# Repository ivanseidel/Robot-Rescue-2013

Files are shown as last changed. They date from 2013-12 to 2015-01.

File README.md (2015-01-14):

Robot-Rescue-2013
=================

RoboCup Rescue B

This repository includes the entire Rescue B project from 2013, used in the international RoboCup Rescue B league.

There is an old version (android based) of it (on the picture, the 2012 one), find out more [here](https://github.com/ivanseidel/Robot-Rescue-2012).

This robot uses two Arm Cortex M3 and one Atmega328. All the code is written in C++, using using Interfaces, and Classes hierarchy to provide well encapsulated code, and easy to use.

Because our team was participating at the same time on the Soccer Junior B league too, we couldn't finish it's code completely, but Mechanics, Hardware and Firmware part was 100% completed. Here is the [Soccer project repository](https://github.com/ivanseidel/Robot-Soccer-2013).

The image bellow is a picture/render of the real robot, and it's project rendered in SolidWorks.

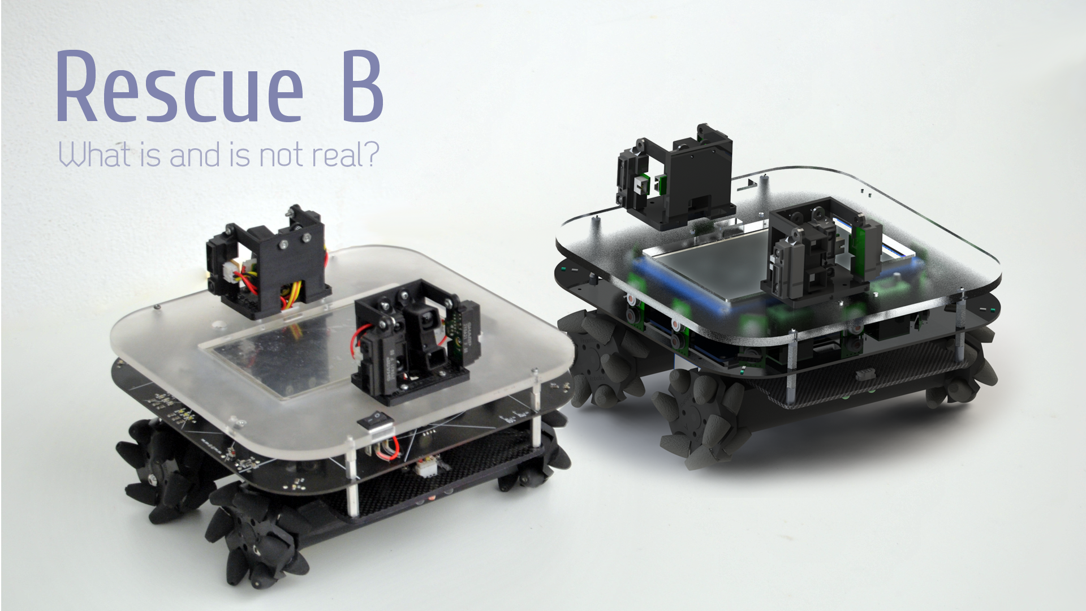
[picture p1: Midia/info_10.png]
RoboCup Rescue B render


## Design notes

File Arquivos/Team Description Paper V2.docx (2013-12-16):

Abstract— This paper presents a description of an omnidirectional robot to be used on the Rescue B competition. The main robot controller was written in C++ and runs in an Arduino DUE board. The Arduino board, that is responsible for the distance and temperature sensors readings, is connected to an MBed board that controls the motor drivers. There are eight infra-red distance sensors mounted on the top of the robot, four of them measuring the distance form the robot and the side walls, two measuring the distance in front of the robot and the other two measuring the distance from the back. The robot mechanical structure was designed using a 3D modeling software and was built using acrylic. It has four omnidirectional wheels that allow the robot to move in any direction without the need of turning itself. The robot was entirely designed, built and programmed by the team students.

# Team Description Paper: Team Emerotecos

Abílio Marcos Coelho de Azevedo¹, André Seidel Oliveira², Ivan Seidel Gomes³, Yan Victor Ribeiro Marim⁴ , Matheus Pimentel Canejo Pinheiro da Cunha⁵, Hudson Cássio Gomes Oliveira⁶, Felipe Nascimento Martins⁷

# I. Introduction

This is to show team Emerotecos’ strategies to solve the challenge proposed to the Rescue B Competition.

To build the robot, we didn’t use any building kit, as we designed the whole robot from sketch, using Dassault Systemes’ Solid Works software [1]. The robot was built basically with 5mm thick acrylic pieces, whose are tough enough for the application.

As the main processor, we use an Arduino DUE boad, which is programmed using C++. We choose the Arduino DUE board because, comparing to the Android mobile phone that we used last year, it is easier to communicate with the motors and sensors as the board has many analogic and digital entries, also using I2C protocol.

# II. Objective

The objective of this project is to build a smart robot that can cross a maze build with wood walls, and identify the electrically heated victims that are placed along the maze’s walls.

# III. Ambient

The Challenge happens in a modular arena, made with wood, which has 2 floors, and 4 main rooms. The location of the walls are always unknown by the time the robot starts running, so that it runs in a real maze. The only constant information about the arena is its total size, what makes it easier to the robot to find its way on the place. An illustration of the maze is shown in Figure 1.

Some heated “victims” are randomly positioned on some walls in the arena, and the robot has to identify them to get points.

In some places, there are some “dead ends”, which are a black mat on the ground. The robot can run over these black mats, but it has to leave it on the same side it came from, it can’t cross the black area.

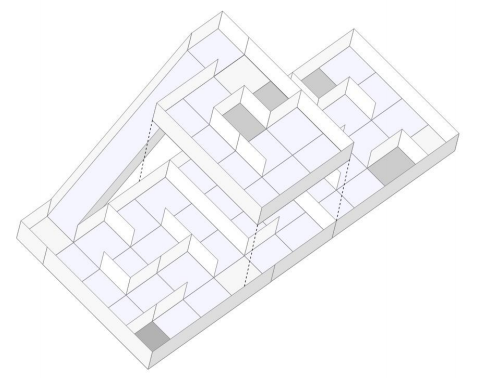
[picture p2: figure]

Rescue B Arena illustration.

# IV. Strategy

## A. Robot Structure

As we participated in this category last year, we built it basically like our first version(figure 4), but with some important improvements that will ensure a better performance is this competition. The robot´s basic composition are 2 acrylic layers, and some acrylic beams. We use a Mecanum omnidirectional wheels system, which makes our robot able to drive to every direction. The Mecanum system works as a regular omni system, and now we´re going to try new suspensions (figure 2) to hold the motors, made of kevlar. Figure 3 shows the robot eletronics design and Figure 1 shows the actual robot.

We use 4 very strong motors, with encoders, so that we can precisely move our robot everywhere. We rely on 4 motors, one for each wheel, because the MECANUM omnidirectional system need different control for each wheel. Each motor can spin giving a 6kgm torque, and its encoder can read up to 3592 pulses per turn because we have a 75:1 speed reduction.


Figure 1 - This year´s Robot

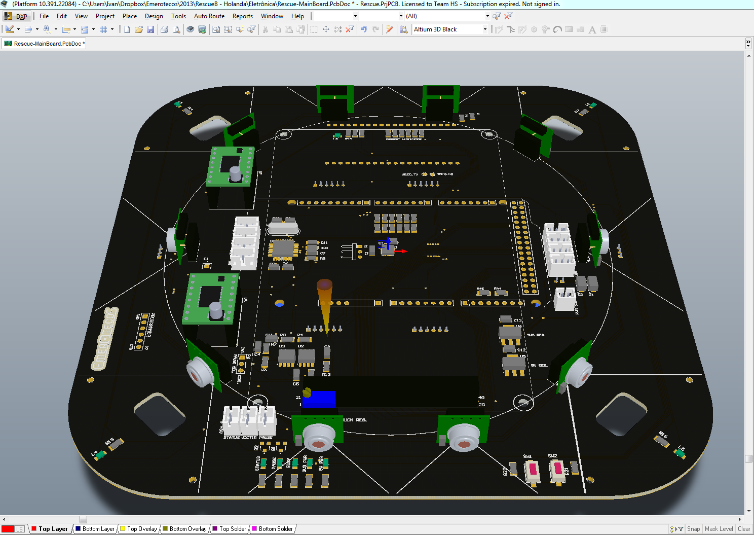
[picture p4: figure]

Figure 3 - Eletronics.

To process the encoder pulses, we have a MBED board, using a ARM Cortex M3, at 100MHz. This board is also responsible for controlling the engines speed. The communication protocol used to read the encoders from the interface, and to set the motors speeds, is the I²C. The MBED board only has 3 encoder inputs. So, we had to program another encoder counter.

To make good measurements with the infrared distance sensors, we’ve made two supports that will accomodade them in the front and back of the robot, to get measurements in every direction. Each support will carry four sensors.

As we use complex algorithms (described latter), we need a very complex processing unit. For this reason we have decided to use an Arduino Due instead of the Android phone used on our last robot. We chose Arduino because its communication with the other controlling systems will be faster. Also, we have an independent touchscreen LCD screen and several sensors, like IMU, so that we can replace the Android facilities. Our sensors gives the robot a very precise way to know it’s position and angle, on all axles, so that we can execute our mapping device with precision and reliability.

As you can see in the Figures 2 and 3, the distance sensors are positioned on rotary base on the top of the robot. This base is driven by a servomotor so that the sensors can be aimed to virtually any direction. Its visible too how are the Mecanum wheels mounted on the robot, similar to a Four by Four car, but with the capacity of moving to any direction without needing to turn.


Figure 2 - Suspension pressure test

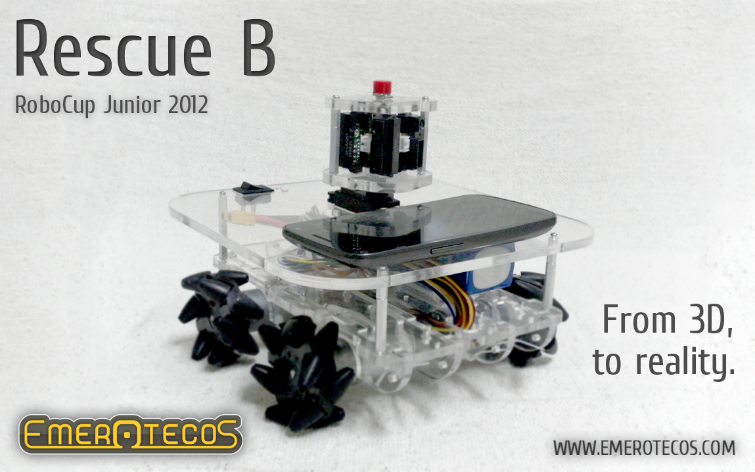
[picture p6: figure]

Figure 4 - Last year robot

## B. Programming

The main controller of our robot is an Arduino Due, witch process the main code and receives information from distance sensors so that it can send the orders to the MBED, that controls the motors.

Last year, the Android phone were used to send and receive data to/from the IOIO, which reads the sensors, and communicates with the MBED board, the one responsible for controlling the motors. Turned out that this configuration was overloading the communication system, so with Arduino we could just take the IOIO board and make a faster contact between sensors and the processing.

Our robot uses 2 types of distance sensors: short distance sensors and long distance ones. That way we can be more precise at taking measurements by the front an back of the robot, as in figure 5.

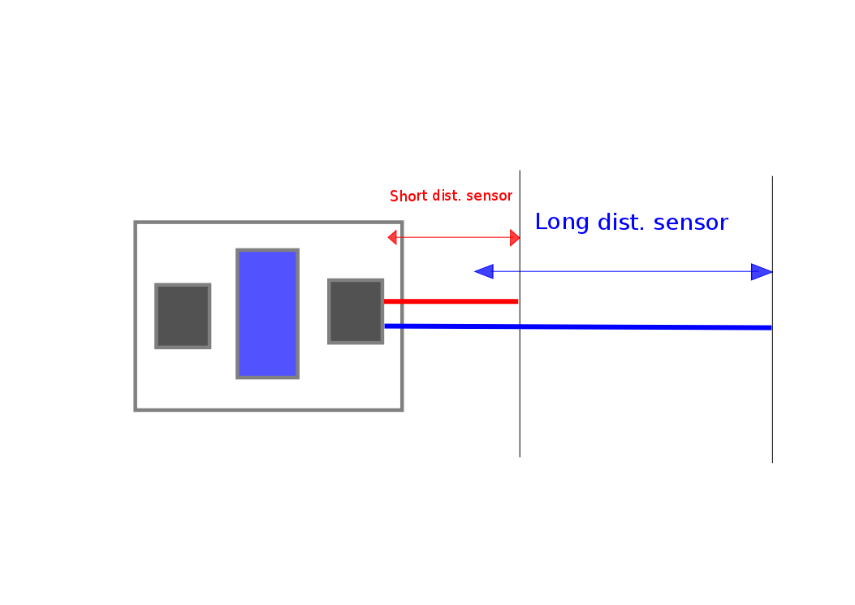
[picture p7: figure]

Figure 5 – Front/back sensors displacement

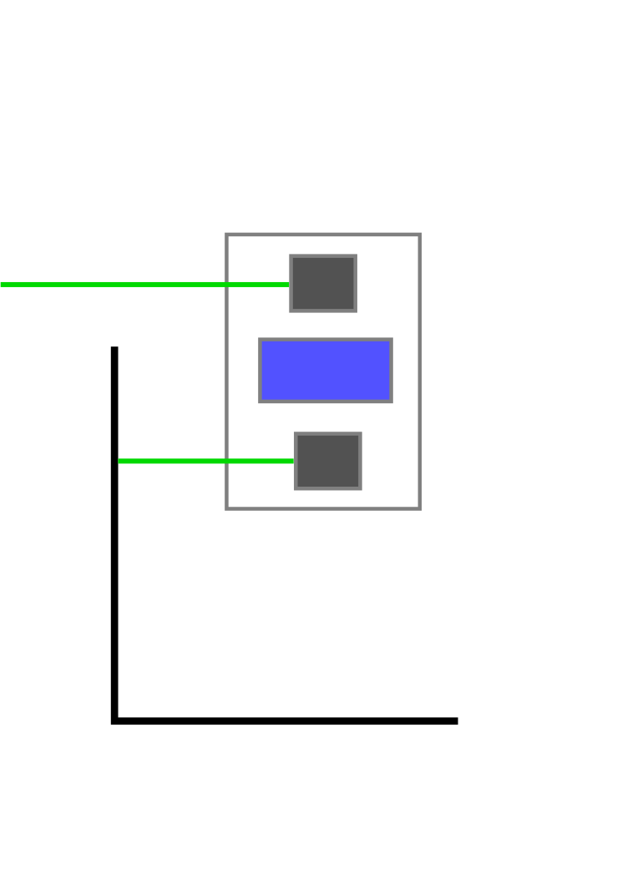
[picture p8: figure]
A description...

We also have heat sensors to detect victims all along the robot borders. The reason of choosing the front/back formation for the sensors supports is because that way the robot will know more accurately the end of any set of walls (figure 6) , so they need to be as far as they can be from each other.

Figure 6 – lateral sensors displacement

The distance measures are also used to correct the robot alignment in order to maintain its correct orientation parallel to the maze walls. This is done by comparing the measures at 20º and -20º from the central line, and calculating the necessary robot turning to make the robot alignment.

To move the robot, we use a simplified kind of SLAM (Simultaneous Localization And Mapping) algorithm, so that we can map the arena. We know that the walls are oriented in only 2 directions (0º and 90º), and we also know that each part of the maze is formed by a 30 x 30 cm square. With this knowledge and using the distance measures obtained via the infrared sensors, we can find out the walls positions and build a map of the maze. The SLAM is programmed in C++, and it runs on the Arduino DUE while the robot is moving in the arena.

We intend to change the algorithm to implement obstacle avoidance and to improve motion control. The idea is to make the robot move continually, with no stops. Last year´s robot succeeded to map, as in Figure 7, but on each block it had to stop, so we are trying to avoid it now. We also intend to attach more heat sensors. Those improvements will be completed by June 2013 for the RoboCupJunior 2013, in Holland.

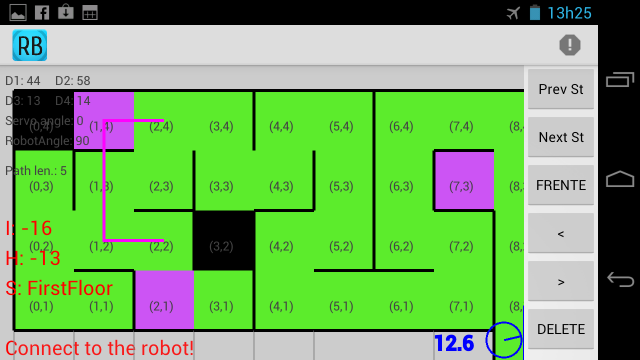
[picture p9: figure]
A description...

Figure 7 - On-line mapping from last year´s robot.

# V. Conclusion

Mapping is the best way to solve this challenge, because it makes it easy to visit every module of the arena, and consequently, find all victims. We have successfully used this robot in the RoboCupJunior 2012 Rescue B competition. A presentation video about the robot is available in [5].

# VI. Acknowledgement

The authors thank the Federal Institute from Espírito Santo (IFES) for all the support given in this project.

# References

[1] 3D CAD Design Software SolidWorks. Available at: http://www.solidworks.com/. Access: Sep. 5, 2012.
[2] Andoid, the world’s most popular mobile platform. Available at: http://developer.android.com/about/index.html. Access: Sep. 5, 2012.
[3] Mbed - Rapid Prototyping for Microcontrollers. Available at: http://mbed.org/. Access: Sep. 5, 2012.
[4] IOIO Documentation. Available at: https://github.com/ytai/ioio/wiki. Access: Sep 5, 2012.
[5] NERA. Prêmio de Melhor Robô do mundo é de alunos do IFES! (com vídeo). Available at http://nera.sr.ifes.edu.br/?p=143. Access: Sep. 5, 2012.

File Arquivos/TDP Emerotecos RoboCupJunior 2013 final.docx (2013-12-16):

# Team Description Paper: Team Emerotecos

Abílio Marcos Coelho de Azevedo, André Seidel Oliveira, Ivan Seidel Gomes, Yan Victor Ribeiro Marim , Matheus Pimentel Canejo Pinheiro da Cunha, Hudson Cássio Gomes Oliveira, Felipe Nascimento Martins

IFES – Federal Institute of Education, Science and Technology of Espirito Santo, Brazil

NERA – Núcleo de Estudos em Robótica e Automação

Abstract— This paper presents a description of an omnidirectional robot to be used on the RoboCupJunior Rescue B competition. The main robot controller was written in C++ and runs in an Arduino DUE board. The Arduino board is responsible for the distance and temperature sensors readings, and is connected to an MBed board that controls the motor drivers. There are eight infra-red distance sensors mounted on the top of the robot, four of them measuring the distance from the robot to the side walls, two measuring distance to obstacles or walls in front of the robot and the other two measuring distance to obstacles or walls in the back. The robot mechanical structure was designed using a 3D modeling software and was built using acrylic. It has four omnidirectional wheels that allow the robot to move in any direction without the need of turning itself. The robot was entirely designed, built and programmed by the team students.

# 1. Introduction

This is to show team Emerotecos’ strategies to solve the challenge proposed by the RoboCupJunior Rescue B competition.

To build the robot, we didn’t use any building kit, as we designed the whole robot from sketch, using Dassault Systemes’ Solid Works software [1]. The robot was built basically with 5mm thick acrylic and carbon fiber pieces, that we found are tough enough for the application.

As the main processor, we use an Arduino DUE board [2], which is programmed using C++. We choose the Arduino DUE board because, comparing to the Android mobile phone that we have used last year, it communicates faster with the motors and sensors as the board has many analogic and digital inputs. It also has support for I²C protocol, which we are using.

# 2. Objective

The objective of this project is to build a smart robot that can cross a maze build with wood walls, and identify the electrically heated victims that are placed along the maze’s walls.

# 3. Ambient

The Challenge happens in a modular arena, made with wood, which has 2 floors, and 4 main rooms. The location of the walls are always unknown by the time the robot starts running, so that it runs in a real maze. The only constant information about the arena is its total size, which makes it easier to the robot to find its way on the place. An illustration of the arena is shown in Figure 1.

Some heated “victims” are randomly positioned on some walls in the arena, and the robot has to identify them in order to score.

In some places, there are some “dead ends”, which are a black mat on the ground. The robot can run over these black mats, but it has to leave it on the same side it came from, it can’t cross the black area.

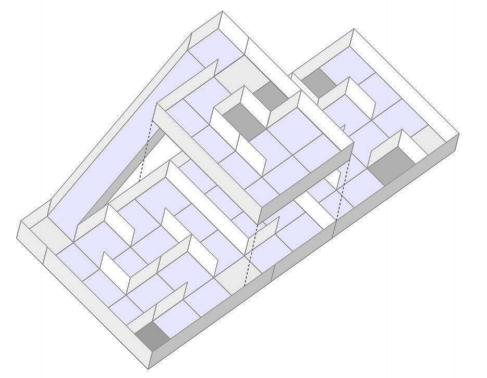
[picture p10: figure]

Fig. 1. Rescue B Arena illustration.

# 4. Strategy

## A. Robot Structure

We have participated in the Rescue B category last year. As our robot had a satisfactory performance, we have decided to build our new robot basically like our first version. Both robots are shown in Figure 2. Although the structure is the same, we have made some important improvements that we hope will ensure a better performance is this year’s competition. The robot’s basic structure is built with an acrylic layer and a carbon fiber layer, with some acrylic beams. We use a Mecanum omnidirectional wheels system, which makes our robot able to move in every direction. Four strong motors, with encoders, drive the robot very precisely. We rely on 4 motors, one for each wheel, because the MECANUM omnidirectional system need independent control for each wheel. Each motor has a torque of 6kgfm, and its encoder can read up to 3,592 pulses per turn because we have a 75:1 speed reduction.

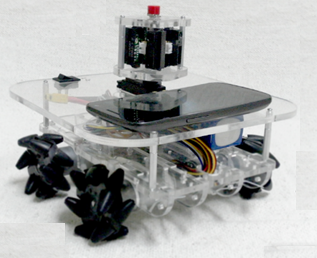
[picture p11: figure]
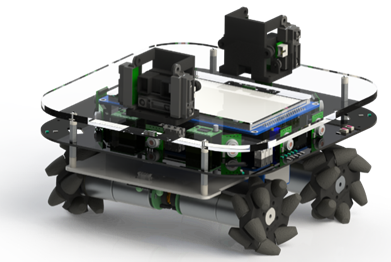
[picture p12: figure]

Fig.2. Last year’s robot (left) and this year´s robot (right).

The Mecanum system works as a regular omni system, and now we’re going to try a new suspension system to hold the motors. This is made of Kevlar and its design is illustrated in Figure 3.

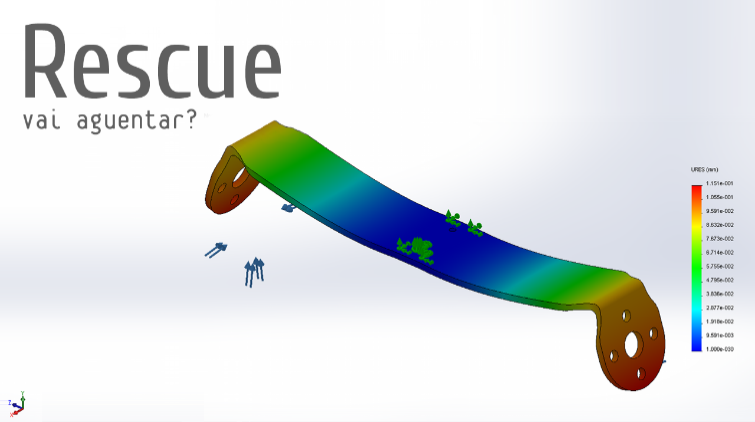
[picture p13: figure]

Fig. 3. Suspension bending simulation.

Figure 4 shows the robot electronics Printed Circuit Board (PCB) design, and Figure 5 presents the actual board already with the LCD placed on top of it. To process the encoder pulses, we have a MBED board [3], with ARM Cortex M3 processor, at 100MHz. This board is also responsible for controlling the motors speed. The communication protocol used to read the encoders from the interface, and to set the motors speeds, is the I²C. The MBED board only has 3 encoder inputs. So, we had to program another encoder counter.


Fig. 4. Eletronics PCB design.

To make good measurements with the infrared distance sensors, we’ve made two supports that will accommodate them in the front and back of the robot, to get measurements in every direction. Each support will carry four sensors.

As we use complex algorithms (described latter), we need a very complex processing unit. For this reason we have decided to use an Arduino Due instead of the Android phone used on our last robot. We chose Arduino because its communication with the other controlling systems will be faster. Figure 6 shows the bottom of the same board, where the Arduino Due and the MBED boards are placed.

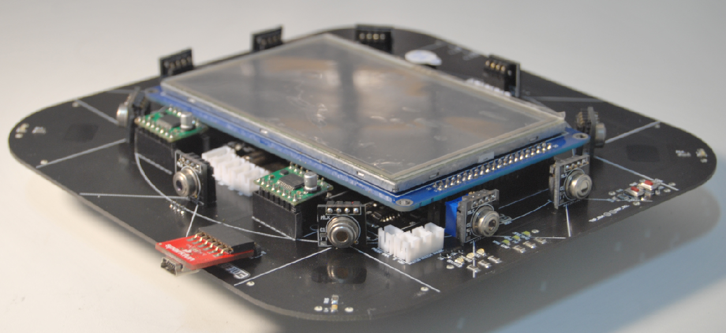
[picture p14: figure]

Fig. 5. Actual PCB (top) with heat sensors and LCD.

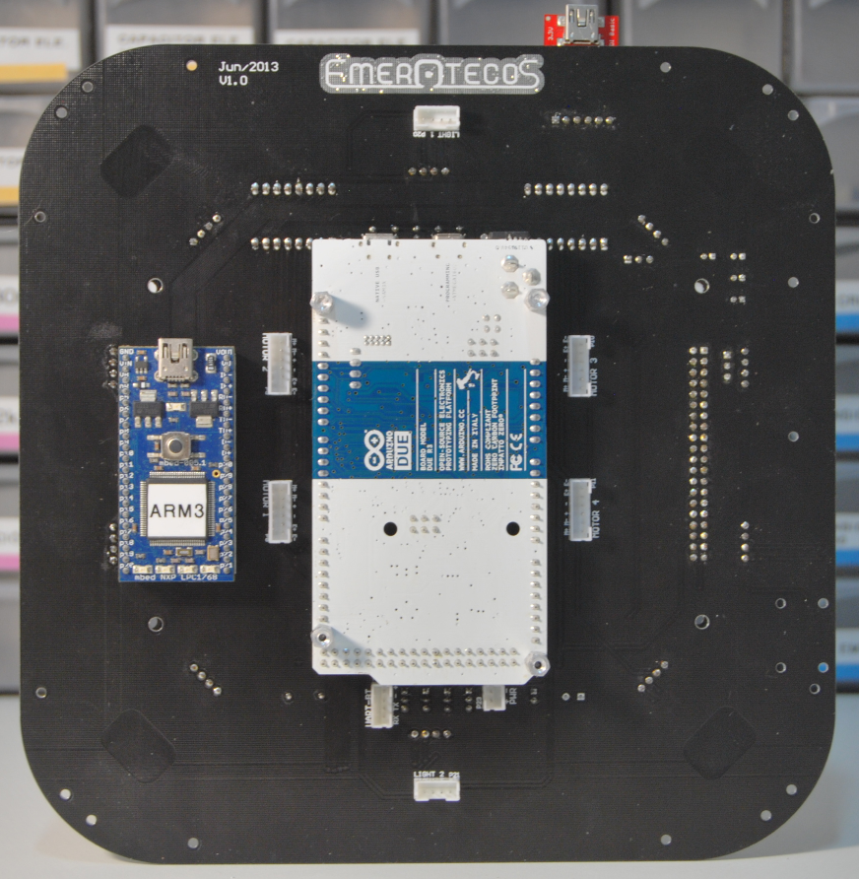
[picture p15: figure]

Fig. 6. Actual PCB (bottom) with Arduino Due and MBED boards.

## B. Programming

The main controller of our robot is an Arduino Due, witch process the main code and receives information from the distance sensors so that it can send commands to the MBED, which controls the motors.

Last year, an Android phone were used to send and receive data to/from an IOIO board [4], which reads the sensors, and communicates with the MBED board, the one responsible for controlling the motors. We have noticed that this configuration was overloading the communication system. To overcome this problem we are suing an Arduino Due instead of the Android phone, and we don’t need the IOIO board, which makes it faster to communicate with sensors and motors.

Our robot uses two types of infrared distance sensors: short distance sensors and long distance ones. Both types are mounted in front and in the back of the robot, pointing in the same direction. This was implemented to improve precision of the distance measurement in these directions (see Figure 7).


Fig. 7. Front/back sensors displacement

We also have heat sensors to detect victims all along the robot borders. The reason of choosing the front/back formation for the sensors supports is because that way the robot will know more accurately the end of any set of walls (figure 8), so they need to be as far as they can be from each other.

A description...

Fig. 8. Lateral sensors displacement

To move the robot, we use a simplified kind of SLAM (Simultaneous Localization And Mapping) algorithm, so that we can map the arena. We know that the walls are oriented in only 2 directions (0º and 90º), and we also know that each part of the maze is formed by a 30 x 30 cm square. With this knowledge and using the distance measures obtained via the infrared sensors, we can find out the walls positions and build a map of the maze. The SLAM is programmed in C++, and it runs on the Arduino DUE while the robot is moving in the arena.

We intend to change the algorithm to implement obstacle avoidance and to improve motion control. The idea is to make the robot move continually, with no stops. Last year´s robot succeeded to map, as shown in Figure 9, but on each block it had to stop to take distance measurements. We are trying to avoid this now. We also intend to attach more heat sensors. Those improvements will be completed by June 2013 for the RoboCupJunior 2013, in Holland.

A description...

Fig. 9. On-line mapping from last year´s robot.

# 5. Conclusion

Mapping is the best way to solve this challenge, because it makes it easy to visit every module of the arena, and consequently, find all victims. We have successfully used this robot in the RoboCupJunior 2012 Rescue B competition. A presentation video about the robot is available in [5]. In RoboCupJunior 2013 Rescue B we intend to succeed in mapping the arena, but now with the SLAM algorithm!

# 6. Acknowledgement

The authors thank the Federal Institute from Espírito Santo (IFES) for all the support given in this project.

# 7. References

[1] 3D CAD Design Software SolidWorks. Available at: http://www.solidworks.com/. Access: Sep. 5, 2012.
[2] Arduino Due. Available at: http://arduino.cc/en/Main/ArduinoBoardDue . Access: Mar. 29, 2013.
[3] MBED - Rapid Prototyping for Microcontrollers. Available at: http://mbed.org/. Access: Sep. 5, 2012.
[4] IOIO Documentation. Available at: https://github.com/ytai/ioio/wiki. Access: Sep 5, 2012.
[5] NERA. Prêmio de Melhor Robô do mundo é de alunos do IFES! (com vídeo). Available at http://nera.sr.ifes.edu.br/?p=143. Access: Sep. 5, 2012.

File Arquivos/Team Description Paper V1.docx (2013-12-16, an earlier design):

[^1]

# Team Description Paper: Team Emerotecos

Abílio Marcos Coelho de Azevedo¹, André Seidel Oliveira², Ivan Seidel Gomes³, Matheus Pimentel Canejo Pinheiro da Cunha⁴, Hudson Cássio Gomes Oliveira⁵, Felipe Nascimento Martins⁶

Abstract— This paper presents a description of an omnidirectional robot to be used on the Rescue B competition. The main robot controller was written in Java and runs in an Android-based mobile phone. The phone is connected to an IOIO board that serves as an interface between the main controller and the robot’s motors and sensors. The IOIO board connects to an Arduino board, that is responsible for the distance and temperature sensors readings, and to an MBed board that controls the motor drivers. There are four infra-red distance sensors mounted on a rotary base on the top of the robot. The base angle is constantly changed by a servomotor, which allows a 360º distance measuring. The robot mechanical structure was designed using a 3D modeling software and was built using acrylic. It has four omnidirectional wheels that allow the robot to move in any direction without the need of turning itself. The robot was entirely designed, built and programmed by the team students.

# I. Introduction

This is to show team Emerotecos’ strategies to solve the challenge proposed to the Rescue B Competition.

To build the robot, we didn’t use any building kit, as we designed the whole robot from sketch, using Dassault Systemes’ Solid Works software [1]. The robot was built basically with 5mm thick acrylic pieces, whose are tough enough for the application.

As the main processor, we use an Android phone, which is programmed using Java. This is a very interesting platform to work with since nowadays Android is the world’s most popular mobile platform [2].

To send the signals from the Android to the motors (that are controlled by an MBED board [3]), we use a board called IOIO, which is responsible for reading all the sensors as well [4].

# II. Objective

The objective of this project is to build a smart robot that can cross a maze build with wood walls, and identify the electrically heated victims that are placed along the maze’s walls.

# III. Ambient

The Challenge happens in a modular arena, made with wood, which has 2 floors, and 4 main rooms. The location of the walls are always unknown by the time the robot starts running, so that it runs in a real maze. The only constant information about the arena, is its total size, what makes it easier to the robot to find its way on the place. An illustration of the maze is shown in Figure 1.

Some heated “victims” are randomly positioned on some walls in the arena, and the robot has to identify them to get points.

In some places, there are some “dead ends”, which are a black mat on the ground. The robot can run over these black mats, but it has to leave it on the same side it came from, it can’t cross the black area.


Figure 1.  Rescue B Arena illustration.

# IV. Strategy

## A. Robot Structure

Our robot is built basically with 2 acrylic layers, and some acrylic beams. We use a Mecanum omnidirectional wheels system, which makes our robot able to drive to every direction. The Mecanum system works as a regular omni system, but it uses 4 tractioned wheels, instead of three, normally used. Figure 2 shows the robot design and Figure 3 shows the actual robot, without the control boards.

We use 4 very strong motors, with encoders, so that we can precisely move our robot everywhere. We rely on 4 motors, one for each wheel, because the MECANUM omnidirectional system need dierent control for each wheel. Each motor can spin giving a 6kgm torque, and its encoder can read up to 3592 pulses per turn because we have a 75:1 speed reduction.

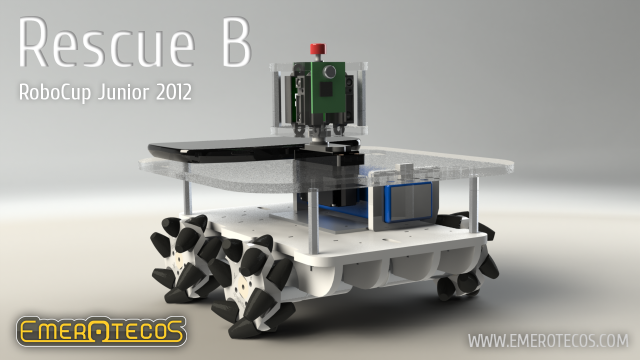
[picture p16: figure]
Info_05

Figure 1.  Robot design.

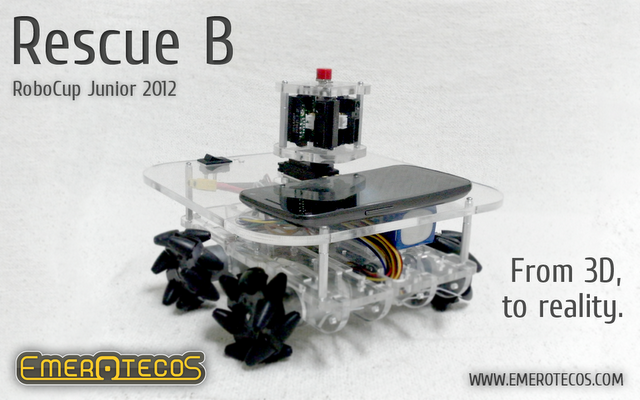
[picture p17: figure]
Info_06

Figure 2.  Robot picture(without control boards).

To process the encoder pulses, we have a MBED board, using a ARM Cortex M3, at 100MHz. This board is also responsible for controlling the engines speed. The communication protocol used to read the encoders from the interface, and to set the motors speeds, is the I²C. The MBED board only has 3 encoder inputs. So, we had to program another encoder counter.

To make good measurements with the infrared distance sensors, we’ve put them in a turnable head over the robot, so that we can make meausures to every direction. To identify the victims, we have 4 thermal infrared sensors strategically positioned around the robot, so that we can measure temperatures in every wall.

As we use complex algorithms (described latter), we need a very complex processing unit. For this reason we have decided to use an Android phone on our robot. Android because we can program using Java. Also, the phone has a touchscreen LCD screen and several sensors we can access. For instance, we make use of the 3 axles gyroscope and 3 axles magnetometer that are present on the Android phone. This gives the robot a very precise way to know it’s position and angle, on all axles.

As you can see in the Figures 2 and 3, the distance sensors are positioned on rotary base on the top of the robot. This base is driven by a servomotor so that the sensors can be aimed to virtually any direction. Its visible too how are the Mecanum wheels mounted on the robot, similar to a Four by Four car, but with the capacity of moving to any direction without the need to turn.

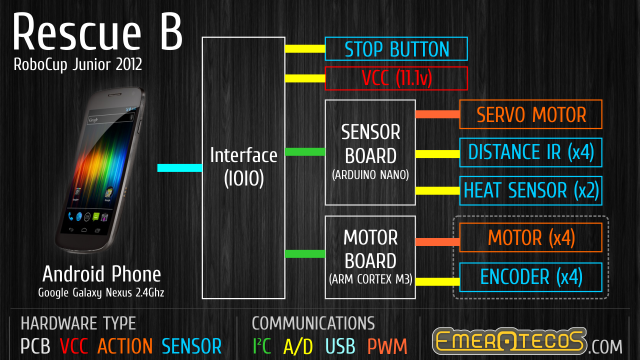
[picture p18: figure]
Info_04

Figure 3.  Control System overview.

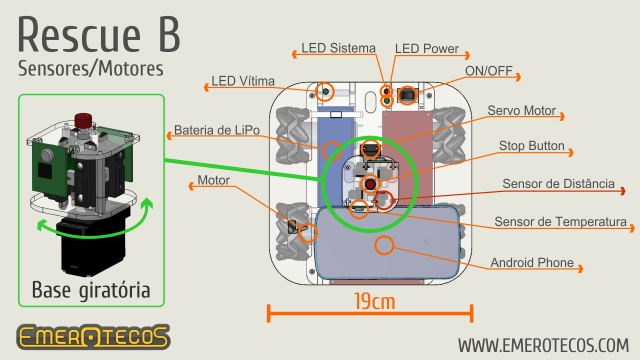
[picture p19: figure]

Figure 4.  Rotary base (left) and top view of the robot.

## B. Programming

The main controller of our robot is an Android cellphone. We choose Android, because it’s an open platform [2], and it’s possible to connect the cellphone with the sensors easily, using the IOIO board [4].

The Android phone sends and receives data to/from the IOIO, which reads the sensors, and communicates with the MBED board, the one responsible for controlling the motors. Figure 4 shows the control system overview.

Our robot uses 2 types of sensors: infrared distance sensor (by Sharp) and heat sensor. The heat sensor is used to detect the victims and are placed on the robot borders. As explained on the previous section, the infrared sensors are mounted on a rotary base. Each one of infrared sensors are pointed 90º from each other in a way that the 4 distance measures can be made at once. The 4 distance measures are repeated several times during a head rotation (one measure per degree) in order to detect the maze walls and obstacles. Figure 5 shows the rotary base with the infrared sensors placed on it, and presents a top view of the robot.

The distance measures are also used to correct the robot alignment in order to maintain its correct orientation parallel to the maze walls. This is done by comparing the measures at 20º and -20º from the central line, and calculating the necessary robot turning to make the robot alignment. Figure 6 illustrates the described idea.

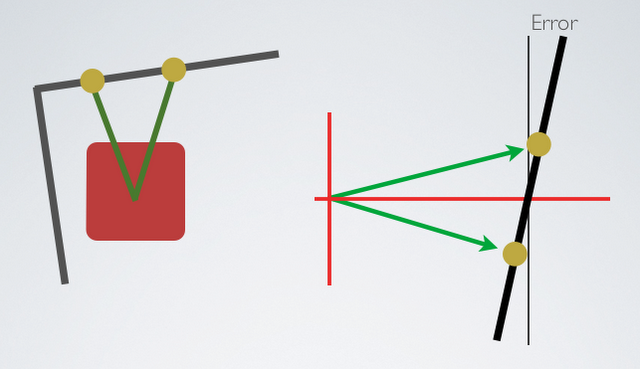
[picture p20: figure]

Figure 5.  Robot design.

To move the robot, we use a simplified kind of SLAM (Simultaneous Localization And Mapping) algorithm, so that we can map the arena. We know that the walls are oriented in only 2 directions (0º and 90º), and we also know that each part of the maze is formed by a 30 x 30 cm square. With this knowledge and using the distance measures obtained via the infrared sensors, we can find out the walls positions and build a map of the maze. The SLAM was programmed in JAVA, and it runs on the Android while the robot is moving in the arena.

While the robot walks around the arena, we can see the map being formed on the cellphone’s screen. Figure 6 shows an example of the mapping screen.


Figure 6.  On-line mapping.

# V. Conclusion

Mapping is the best way to solve this challenge, because it makes it easy to visit every module of the arena, and consequently, find all victims. We have successfully used this robot in the RoboCupJunior 2012 Rescue B competition. A presentation video about the robot is available in [5].

We pretend to change the algorithm to work with obstacles and also do a big improvement on motion of the robot moving continually, with no stops. Attach more infrared distance sensors, well located on the robot, so that they don`t need to rotate.

Those improvement will be done until June 2013 for the RoboCupJunior in Holland.

# VI. Acknowledgement

The authors thank the following companies for the financial support that allowed the robot construction and participation at the 2012 RoboCup and CBR competitions: Proesi Componentes Eletrônicos, Nova Didacta, InTechno Desenvolvimento e Capacitação, Copy Express, Produtiva Hailtools, Use Móveis para Escritórios and Qualidata. They also thank IFES for the support and FAPES (a foundation of the Secretary of Science and Technology of the State of Espirito Santo, Brazil) for the financial support to pay for the air tickets and travel expenses to Fortaleza – LARC 2012 (Project 57768773/2012).

# References

[1] 3D CAD Design Software SolidWorks. Available at: http://www.solidworks.com/. Access: Sep. 5, 2012.
[2] Andoid, the world’s most popular mobile platform. Available at: http://developer.android.com/about/index.html. Access: Sep. 5, 2012.
[3] Mbed - Rapid Prototyping for Microcontrollers. Available at: http://mbed.org/. Access: Sep. 5, 2012.
[4] IOIO Documentation. Available at: https://github.com/ytai/ioio/wiki. Access: Sep 5, 2012.
[5] NERA. Prêmio de Melhor Robô do mundo é de alunos do IFES! (com vídeo). Available at http://nera.sr.ifes.edu.br/?p=143. Access: Sep. 5, 2012.

[^1] The authors are with the Federal Institute of Education, Science and Technology of Espírito Santo (IFES). Rodovia ES-010, km 6,5 - Manguinhos, Serra, ES. abilio_azevedo@hotmail.com¹, aseideloliveira@gmail.com², ivanseidel@gmail.com³, pimentelcanejo@hotmail.com⁴, hudsoncassio@ifes.edu.br⁵, felipemartins@ifes.edu.br⁶.

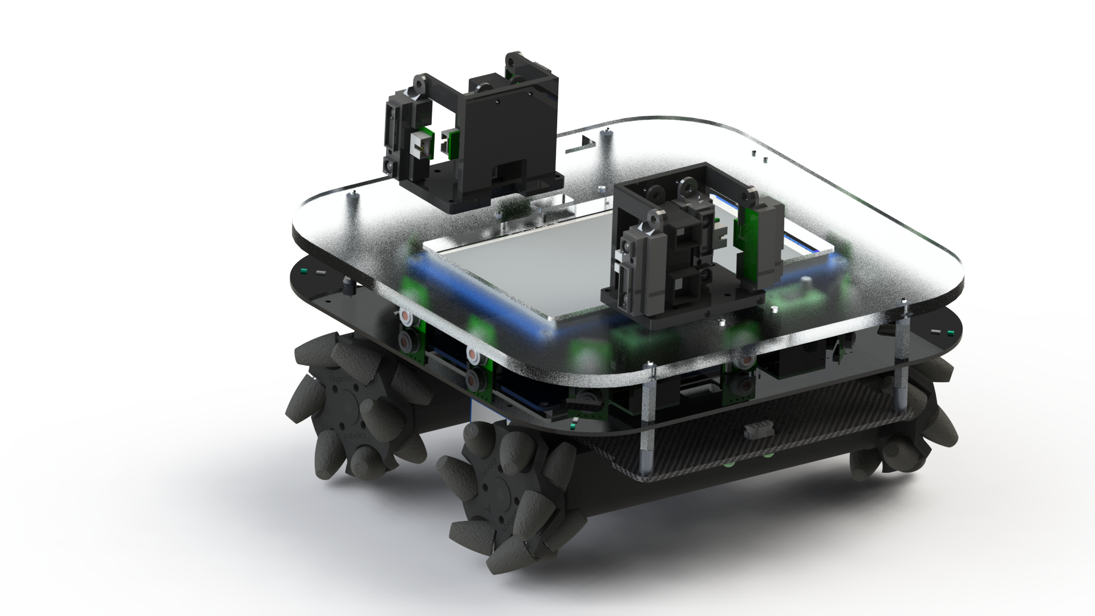
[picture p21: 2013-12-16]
Midia/robot_07.tif

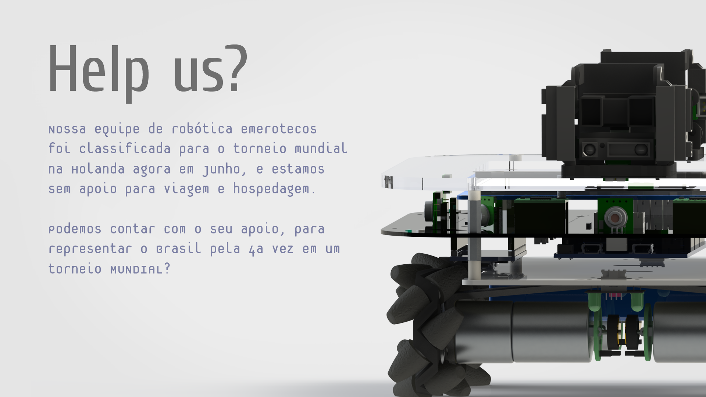
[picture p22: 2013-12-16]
Midia/info_07.png

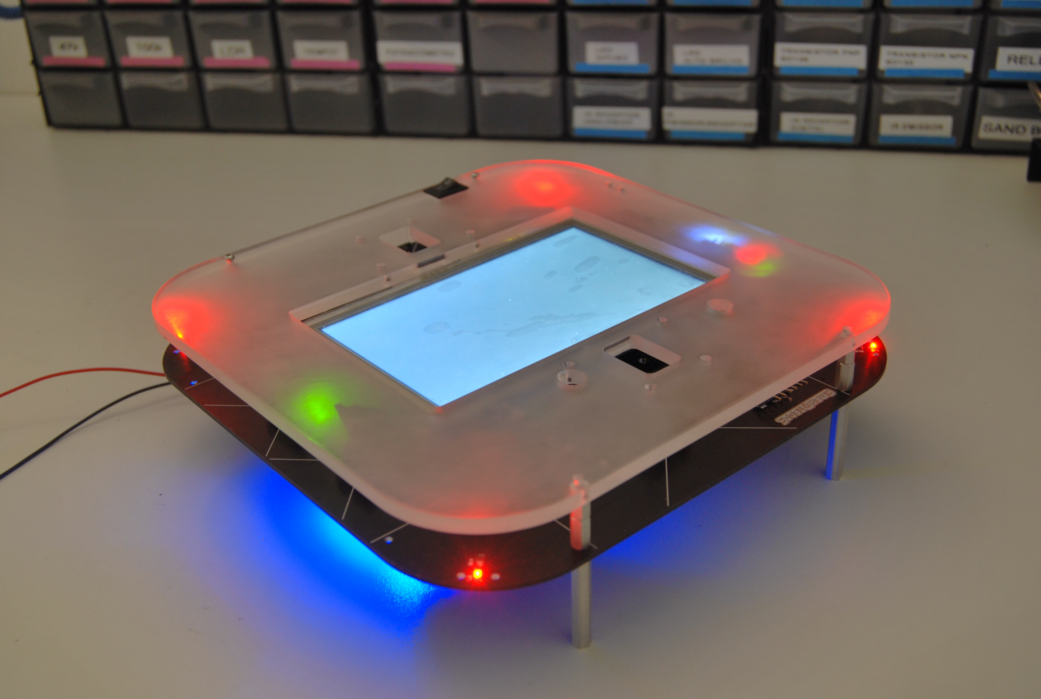
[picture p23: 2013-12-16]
Midia/Fotos/RescueB (19).JPG

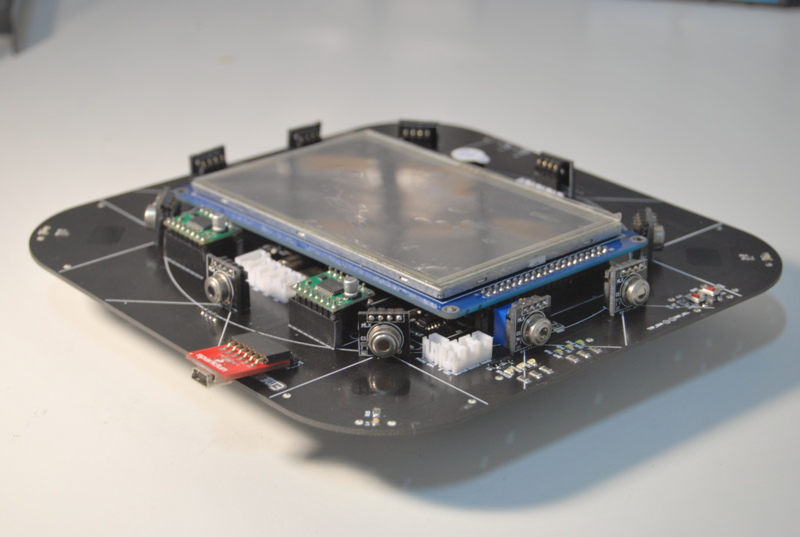
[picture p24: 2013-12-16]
Midia/Fotos/RescueB (8).JPG

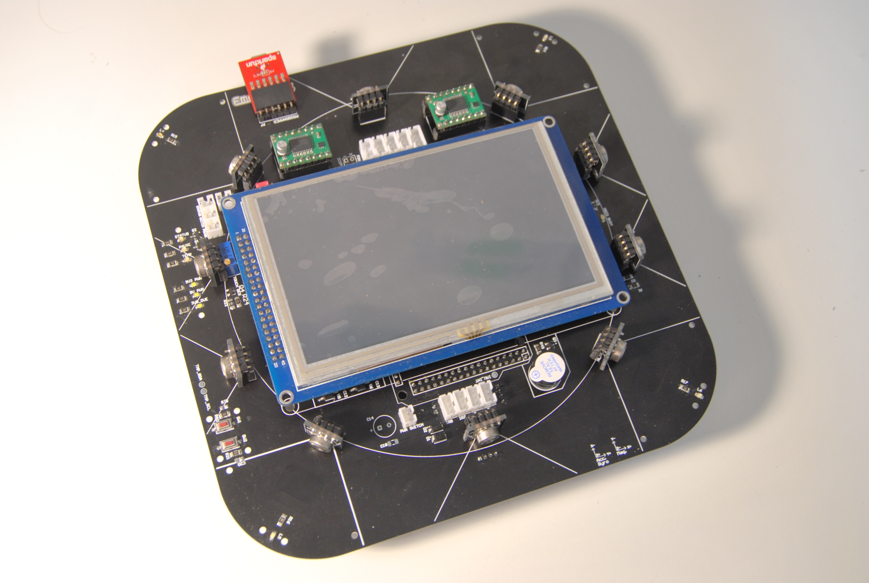
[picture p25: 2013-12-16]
Midia/Fotos/RescueB (6).JPG

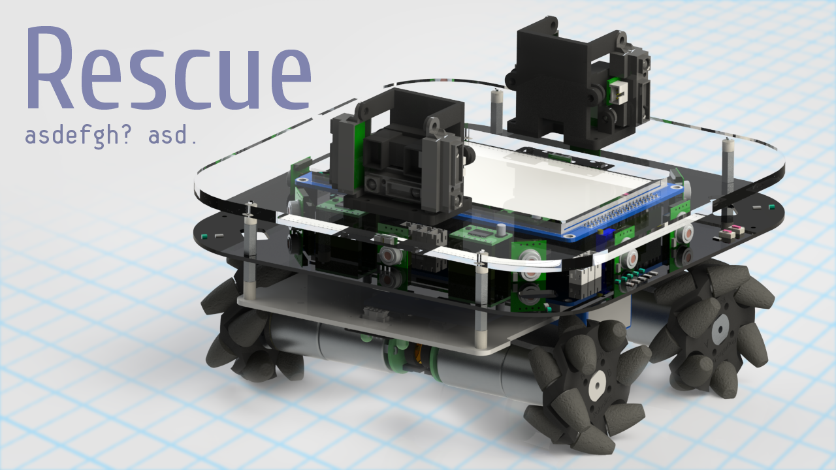
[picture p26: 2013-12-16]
Midia/info_06.png

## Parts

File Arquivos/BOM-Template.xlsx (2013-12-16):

PLANILHA DE CUSTOS - RESCUE B 2013 |  |  |  |  |  | TOTAL | R$3151.81
 |  |  |  |  |  | Dolar: | $2.20
Descrição | Fornecedor | Qtd | Extra | Valor | Imposto | Dolar? | Subtotal | Link
Standoffs (13 mm) FF | pololu | 3 | 1 | 1.79 | 70% | s | R$26.78 | http://www.pololu.com/catalog/product/2091
Standoffs (13 mm) MF | pololu | 3 | 1 | 1.39 | 70% | s | R$20.79 | http://www.pololu.com/catalog/product/1948
LCD TFT 5" | Dealextreme | 0 | 1 | 54.50 | 70% | s | R$203.83 | http://dx.com/p/800-x-480-5-0-lcd-tft-touch-screen-module-w-stylus-pen-for-arduino-blue-154505
Capacitores, Resistores, Transistores, IC's (Faltantes) | Dealextreme | 1 | 0
Bateria Lipo 1.6A 40C 2S 7.4v | HobbyKing | 4 | 0 | 9.49 | 70% | s | R$141.97 | http://www.hobbyking.com/hobbyking/store/__10278__Turnigy_2200mAh_2S_40C_Lipo_Pack.html
IMU InveSense (MPU-9150) | InveSense | 1 | 1 | 17.00 | 70% | s | R$127.16 | http://www.invensense.com/mems/gyro/mpu9150.html
Shipping | InveSense | 1 | 0 | 53.95 | 70% | s | R$201.77
xBee | Itead | 1 | 1 | 13.20 | 70% | s | R$98.74 | http://dx.com/p/xbee-arduino-bluetooth-wireless-module-with-bee-adapter-136423
Circuito Impresso - 10 unidades, 20cm x 20cm, Dupla Face, 1.6mm | Itead | 1 | 0 | 114.00 | 70% | s | R$426.36 | http://imall.iteadstudio.com/open-pcb/pcb-prototyping/im120418010.html
Circuito (para sensores de temp.) - 5cm x 5cm | itead | 1 | 0 | 15.00 | 70% | s | R$56.10 | http://imall.iteadstudio.com/open-pcb/pcb-prototyping/im120418004.html
Rodas Omni | Matheus | 8 | 1 | 0.00 |  |  | R$0.00
Base em alumínio | Matheus | 2 | 2 | 0.00 |  |  | R$0.00
Motores 25D (34:1) | Pololu | 4 | 1 | 34.95 | 70% | s | R$653.57 | http://www.pololu.com/catalog/product/2284 (http://www.pololu.com/catalog/product/1572)
Capacitores, Resistores, Transistores, IC's (Patrocínio) | Proesi | 0 | 0 | 0.00 |  |  | R$0.00
Arduino DUE | SparkFun | 1 | 1 | 49.95 | 70% | s | R$373.63 | https://www.sparkfun.com/products/11589
Mbed | SparkFun | 0 | 1 | 59.95 | 70% | s | R$224.21 | https://www.sparkfun.com/products/9564
Sensor Temp. | Sparkfun | 7 | 1 | 19.95 | 70% | s | R$596.90 | https://www.sparkfun.com/products/9570

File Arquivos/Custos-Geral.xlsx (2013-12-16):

Gastos individuais | Valor por pessoa | Subtotal
Passagem | R$4000.00 | R$20000.00
Hospedagem | R$1500.00 | R$7500.00
Alimentação | R$1000.00 | R$5000.00
Transporte | R$100.00 | R$500.00
Camiseta | R$150.00 | R$750.00
Gastos gerais |  | Subtotal
Material de transporte |  | R$1000.00
Componentes e peças para o Robô |  | R$5000.00
Material de divulgação (Folders, Adesivos…) |  | R$250.00
 | Total: | R$40000.00
Registro | http://www.regonline.com/Register/Checkin.aspx?EventID=1198240
Hotel

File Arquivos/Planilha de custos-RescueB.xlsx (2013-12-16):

PLANILHA DE CUSTOS - RESCUE B 2014 |  |  |  |  |  |  | TOTAL | R$2941.73 |  | Pololu
 |  |  |  |  |  |  | Dolar: | $2.20 |  | R$1305.67
OK | Descrição | Fornecedor | Qtd | Extra | Valor | Imposto | Dolar? | Subtotal | Link
s | LCD TFT 5" | Dealextreme | 1 | 1 | 54.50 |  | s | R$239.80 | http://dx.com/p/800-x-480-5-0-lcd-tft-touch-screen-module-w-stylus-pen-for-arduino-blue-154505
s | Bluetooth | Dealextreme | 1 | 0 | 11.70 |  | s | R$25.74 | http://dx.com/p/bluetooth-master-uart-board-communication-module-blue-152175
s | Capacitores 0805 | Dealextreme | 2 | 0 | 7.60 |  | s | R$33.44 | http://dx.com/p/smd-0805-capacitors-white-20-x-30-pcs-152739
s | Capacitor 1206 10uF | Dealextreme | 1 | 0 | 4.80 |  | s | R$10.56 | http://dx.com/p/avx-1206-smd-10uf-16v-type-a-tantalum-capacitors-30-pcs-148546
s | Capacitores Eletrolitico | Dealextreme | 1 | 0 | 8.60 |  | s | R$18.92 | http://dx.com/p/2-2-470uf-electrolytic-capacitor-assortment-kit-16-50v-100-pcs-156107
s | Bateria Lipo 1.8A 40C 2S 7.4v | HobbyKing | 4 | 0 | 9.49 |  | s | R$83.51 | http://www.hobbyking.com/hobbyking/store/__10289__Turnigy_1800mAh_2S_40C_Lipo_Pack.html
s | Shipping | HobbyKing | 1 | 0 | 17.95 |  | s | R$39.49
s | IMU InveSense (MPU-9150) | InveSense | 1 | 1 | 17.00 | 70% | s | R$127.16 | http://www.invensense.com/mems/gyro/mpu9150.html
s | Shipping | InveSense | 1 | 0 | 53.95 | 70% | s | R$201.77
s | Circuito Impresso - 10 unidades, 20cm x 20cm, Dupla Face, 1.6mm | Itead | 1 | 0 | 114.00 | 70% | s | R$426.36 | http://imall.iteadstudio.com/open-pcb/pcb-prototyping/im120418010.html
s | Circuito (para sensores de temp.) - 5cm x 5cm | itead | 1 | 0 | 15.00 | 70% | s | R$56.10 | http://imall.iteadstudio.com/open-pcb/pcb-prototyping/im120418004.html
s | Shipping | Itead | 1 | 0 | 40.00 | 70% | s | R$149.60
s | Distance IR (4-40cm) | LabDeGaragem | 2 | 1 | 68.10 |  |  | R$204.30 | https://www.sparkfun.com/products/8959
s | Shipping | LabDeGaragem | 1 | 0 | 19.30 |  |  | R$19.30
s | Standoffs (9.5 mm) FF | Pololu | 1 | 2 | 1.69 | 70% | s | R$18.96 | http://www.pololu.com/catalog/product/2084
s | Standoffs (6 mm) MF | Pololu | 1 | 2 | 1.29 | 70% | s | R$14.47 | http://www.pololu.com/catalog/product/1940
s | Standoffs (10 mm) MF | Pololu | 1 | 2 | 1.29 | 70% | s | R$14.47 | http://www.pololu.com/catalog/product/1941
s | Motores 25D (34:1) | Pololu | 0 | 1 | 34.95 | 70% | s | R$130.71 | http://www.pololu.com/catalog/product/2286
s | Arduino DUE | Pololu | 0 | 1 | 49.95 | 70% | s | R$186.81 | http://www.pololu.com/catalog/product/2193
s | Mbed | Pololu | 0 | 0 | 59.00 | 70% | s | R$0.00 | http://www.pololu.com/catalog/product/2150
s | Sensor Temp. | Pololu | 5 | 3 | 19.95 | 70% | s | R$596.90 | http://www.pololu.com/catalog/product/1061
s | Distance IR (20-150cm) | Pololu | 2 | 1 | 14.95 | 70% | s | R$167.74 | http://www.pololu.com/catalog/product/1137
s | Shipping | Pololu | 1 | 0 | 46.95 | 70% | s | R$175.59
s | Capacitores, Resistores, Transistores, IC's (Patrocínio) | Proesi | 0 | 0 | 0.00 |  |  | R$0.00

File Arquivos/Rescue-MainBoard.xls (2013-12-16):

 |  | Rescue-MainBoard.PrjPCB | Rescue-MainBoard.PrjPCB |  |  | 03/04/2013
 |  | PLANILHA DE CUSTOS | Bill of Materials For Project [Rescue-MainBoard.PrjPCB] (No PCB Document Selected) |  |  |  |  |  |  |  | TOTAL | R$0.00
 |  |  |  |  |  |  |  |  |  |  | Dolar: | $2.20
Colunas1 | Colunas2 | LibRef | Footprint | Comment | Designator | Description | Quantity | Extra | Valor | Imposto | Dolar? | Subtotal | Link
 | s | LM358D | 751-02_N | LM358D | U3 | Dual Low-Power Operational Amplifier | 1 | 1 | 0.00
 | s | BUZZER | BUZZER | Buzzer | BZ1 | Buzzer | 1 | 0 | 0.00
s |  | Cap Semi | C0805 | 100nF | C19, C20 | Capacitor (Semiconductor SIM Model) | 2 |  | 0.00
s |  | Cap Semi | C0805 | 0.1uF | C1, C6, C7, C8, C15 | Capacitor (Semiconductor SIM Model) | 5 |  | 0.00
s |  | Cap Semi | C0805 | 2.2nF | C2 | Capacitor (Semiconductor SIM Model) | 1 |  | 0.00
s |  | Cap Semi | C0805 | 100pF | C3, C4, C5, C11 | Capacitor (Semiconductor SIM Model) | 4 |  | 0.00
s |  | Cap Semi | C0805 | 22pF | C9, C10 | Capacitor (Semiconductor SIM Model) | 2 |  | 0.00
s |  | Cap Semi | C0805 | 10nF | C16 | Capacitor (Semiconductor SIM Model) | 1 |  | 0.00
s |  | Cap Semi | C1206 | 10uF | C12, C13, C17, C18 | Capacitor (Semiconductor SIM Model) | 4 |  | 0.00
s |  | EKA00PB310J00 | CAPPR3.5-8X11.5 | 470uF | C14 | Aluminum Electrolytic Capacitor, Radial Style with Long Leads: 100uF, 63V | 1 |  | 0.00
s |  | DIODE | DIODESMA | 1N4004 | D1, D2 |  | 2 |  | 0.00
s |  | Header 3X2 | HDR2X3 | Header 3X2 | P26 | Header, 3-Pin, Dual row | 1 |  | 0.00
 | s | LED | LED0805 | LED | 3V3_1, 3V3_DUE, 5V_1, L1, L2, L3, L4, L5, L6, L7, L8 |  | 11 | 29 | 0.00
 | s | LM555CM | M08A_N | LM555CM | U2 | Timer, 8-pin Narrow SOIC | 1 | 2 | 0.00
 | s | LM1117IMPX-5.0/NOPB | MP04A_N | LM1117IMPX-5.0/NOPB | U5 | 800mA Low-Dropout Linear Regulator, 4-pin SOT-223, Pb-Free | 1 |  | 0.00
 | s | LM1117IMPX-3.3/NOPB | MP04A_N | LM1117IMPX-3.3/NOPB | U6 | 800mA Low-Dropout Linear Regulator, 4-pin SOT-223, Pb-Free | 1 |  | 0.00
 | s | OSC-2-PIN | OSC-2-PIN-TH | 16Mhz | Y1 | 2 pin oscilator | 1 |  | 0.00
s | s | RES | RES1206 | 10K | R1, R2, R5, R6, R9, R10, R12, R20, R21, R24, R32, R34, R36, R38, R40, R42, R44, R46, R47, R49 |  | 20 |  | 0.00
 | s | RES | RES1206 | 100K | R3, R4 |  | 2 |  | 0.00
 | s | RES | RES1206 | 2K2 | R7, R11, R33, R35, R37, R39, R41, R43, R45 |  | 9 |  | 0.00
s |  | RES | RES1206 | 330R | R8, R13, R14, R15, R16, R17, R18, R19, R30, R48 |  | 10 |  | 0.00
 | s | RES | RES1206 | 10R | R22 |  | 1 |  | 0.00
s |  | RES | RES1206 | 1K | R31 |  | 1 |  | 0.00
 | s | BSS138 | SOT23 | BSS138 | Q1, Q2, Q3, Q4 | N-Channel Enhancement Mode Vertical DMOS FET | 8 | 8 | 0.00
 | s | LDR |  |  |  |  | 2 | 2
 | s | LED Alto Brilo Branco |  |  |  |  | 4 | 4
 | s | TRIMPOT | TRIMPOT-3296W | 10K | P4 |  | 1 | 2 | 0.00

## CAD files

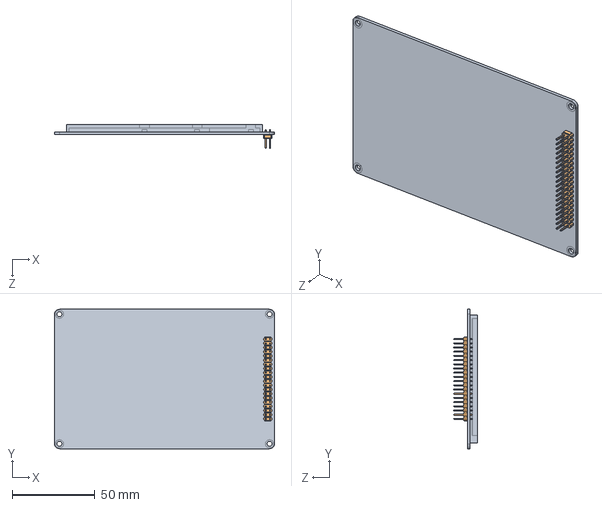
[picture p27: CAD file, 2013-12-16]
Mecânica/Eletrônica/TFT 5.0 touch screen.SLDASM
133.0 x 84.3 x 14.4 mm
TFT 5.0 touch screen
User Library-TFT 3.2 with touch screen_User Library-PLD-40

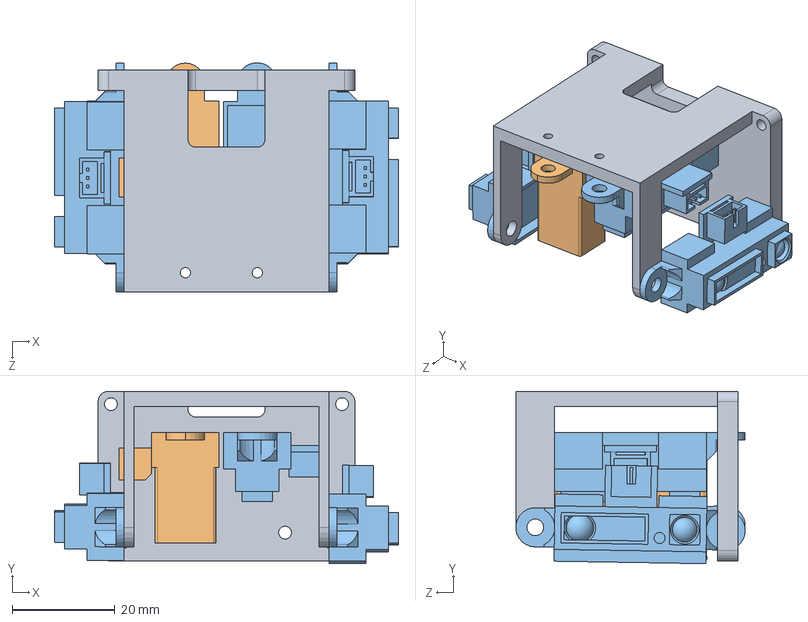
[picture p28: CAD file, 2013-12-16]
Mecânica/Montagens/sensores2.SLDASM
67.0 x 33.6 x 44.7 mm
Ssuporte Sensor2
User Library-IR sensor-1
Sharp_ir_sensor x 3

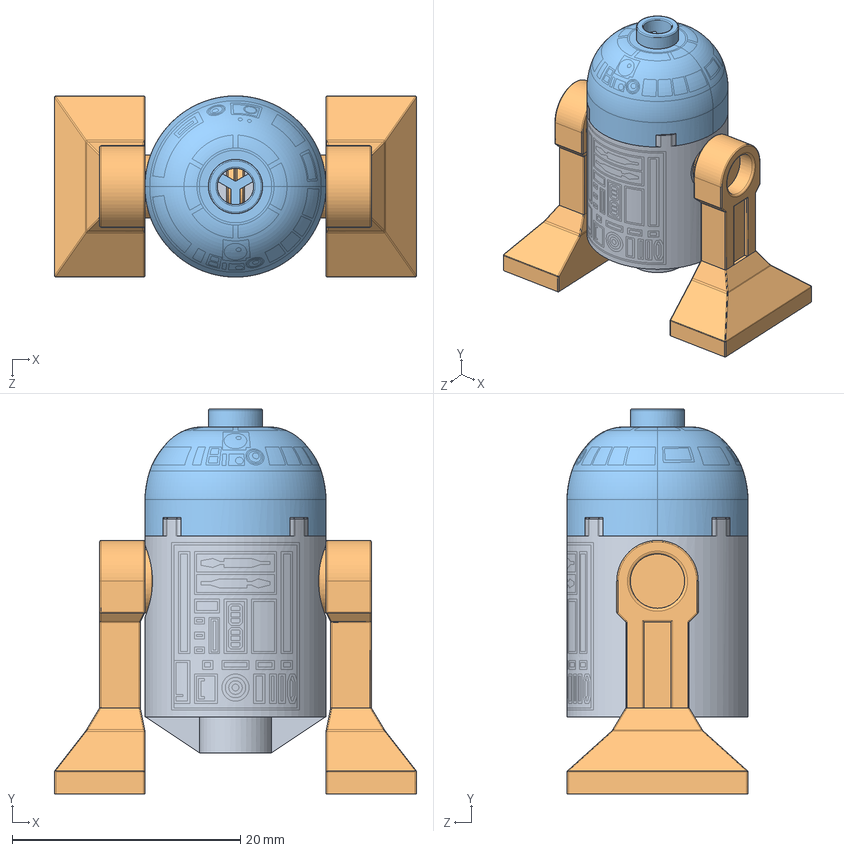
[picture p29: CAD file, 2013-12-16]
Mecânica/Fun/User Library-R2-D2.SLDASM
31.8 x 33.7 x 15.9 mm
User Library-R2-D2_30361PS1
User Library-R2-D2_30362 x 2
User Library-R2-D2_553PS1

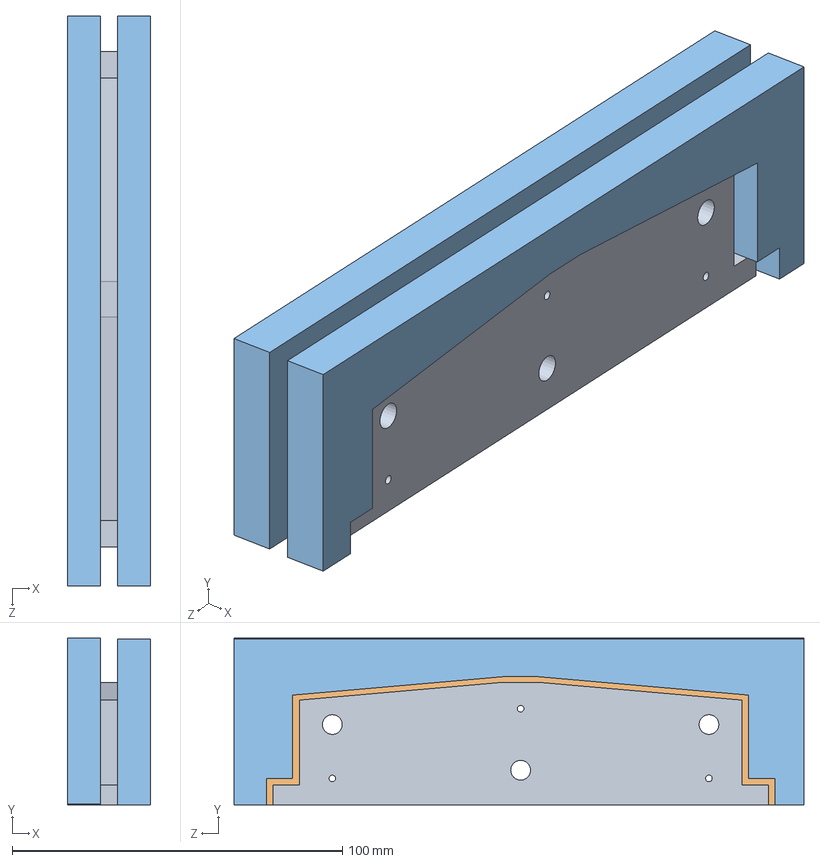
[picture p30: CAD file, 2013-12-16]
Mecânica/molde suspensao/montagemmolde.SLDASM
25.0 x 50.5 x 172.5 mm
molde.suspensao
molde.suspensao2
molde.suspensao.cobertura x 2

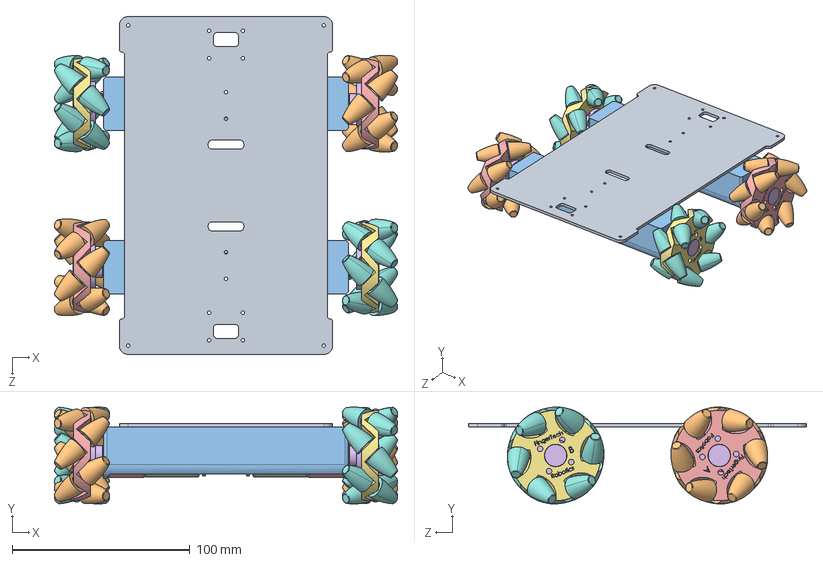
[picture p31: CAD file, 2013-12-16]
Mecânica/Montagens/Chassi.SLDASM
193.1 x 54.5 x 190.0 mm
Chassi
rubber roller x 24
steel pin x 12
Flat Washer Type A Narrow_AI_FW 0.125 x 24
Mecanum Hub A R2 x 2
Cilindro x 4
Mecanum Hub Mirrored B R2 x 2
rubber roller_1 x 24
steel pin_1 x 12
Flat Washer Type A Narrow_AI_FW 0.125_1 x 24
Suspensao_plastico x 2
Motor x 4
Motor_Redutor x 4
Encoder x 4

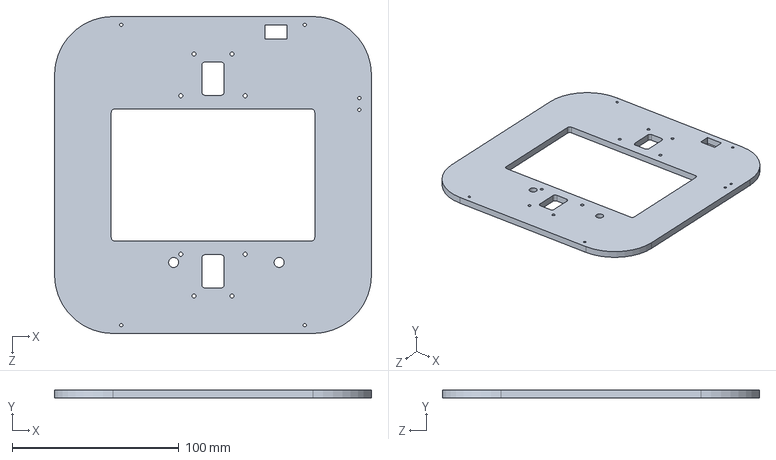
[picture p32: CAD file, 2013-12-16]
Mecânica/Montagens/Camada Superior.SLDASM
190.0 x 5.00 x 190.0 mm

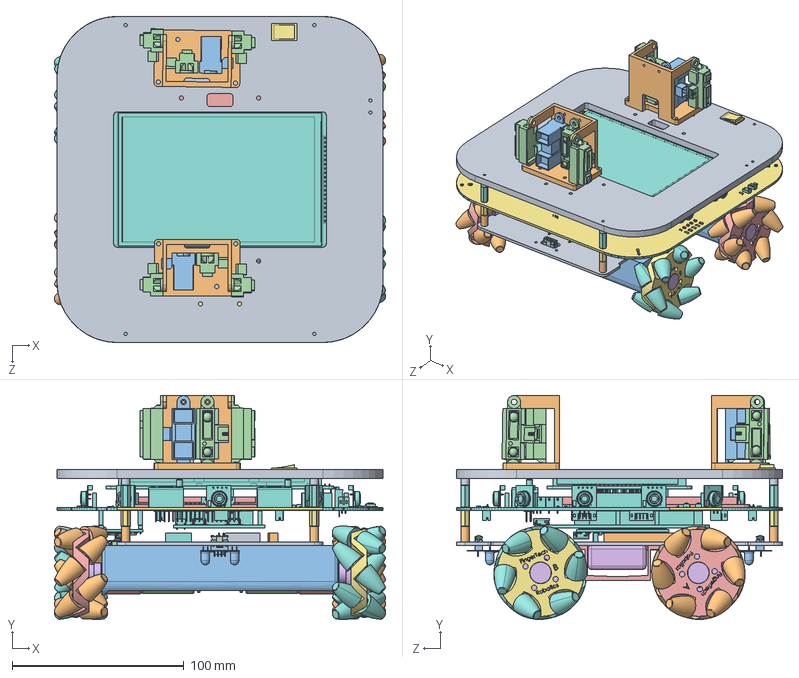
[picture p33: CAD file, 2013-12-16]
Mecânica/Robô_03.SLDASM
193.1 x 130.6 x 190.0 mm
Chassi
rubber roller x 24
steel pin x 12
Flat Washer Type A Narrow_AI_FW 0.125 x 24
Mecanum Hub A R2 x 2
Cilindro x 4
Mecanum Hub Mirrored B R2 x 2
rubber roller_1 x 24
steel pin_1 x 12
Flat Washer Type A Narrow_AI_FW 0.125_1 x 24
Suspensao_plastico x 2
Motor x 4
Motor_Redutor x 4
Encoder x 4
PC-Standoff - 13mm - FF x 4
PC-Standoff - 13mm x 4
Espacador-Top x 4
Espacador-Bottom x 4
Light Sensor Breakout x 2
PHR-4 x 2
Rescue-MainBoard
Proteção
Ssuporte Sensor2 x 2
User Library-IR sensor-1 x 2
Sharp_ir_sensor x 6
suporte.bateria x 2
Bateria-Lipo2
Botão

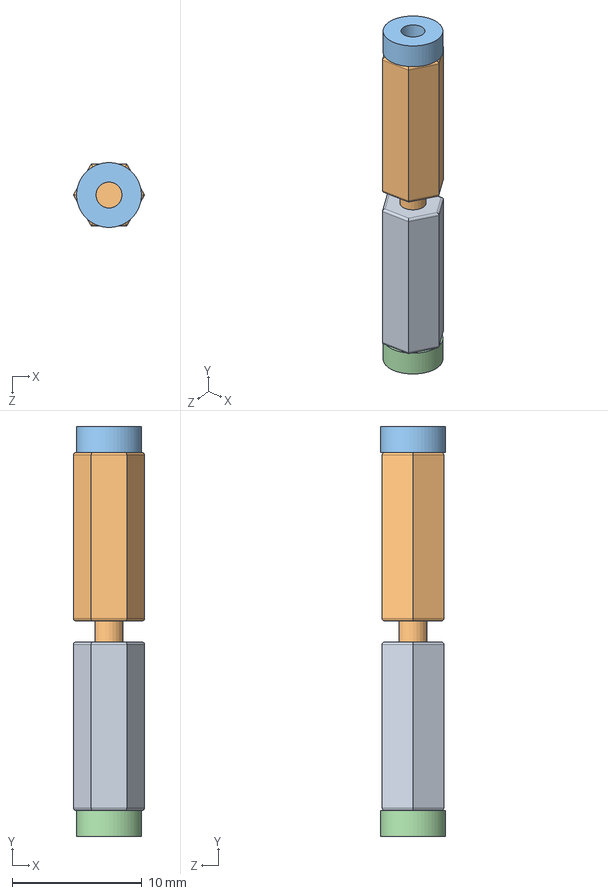
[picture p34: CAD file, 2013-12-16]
Mecânica/Montagens/Standoff.SLDASM
5.50 x 31.6 x 5.00 mm
PC-Standoff - 13mm - FF
PC-Standoff - 13mm
Espacador-Top
Espacador-Bottom

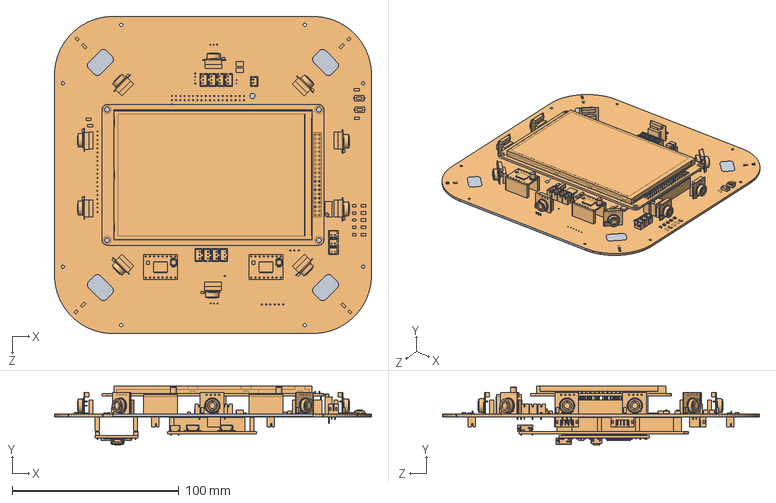
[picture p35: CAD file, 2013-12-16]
Mecânica/Montagens/Eletronica.SLDASM
190.0 x 35.3 x 190.0 mm

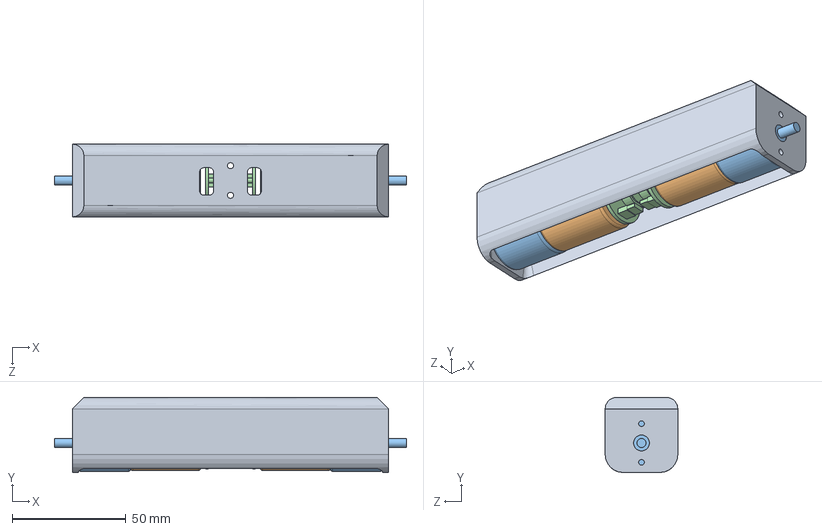
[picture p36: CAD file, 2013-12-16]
Mecânica/Montagens/Suspensao_plastico.SLDASM
154.8 x 33.0 x 32.0 mm
Suspensao_plastico
Motor x 2
Motor_Redutor x 2
Encoder x 2

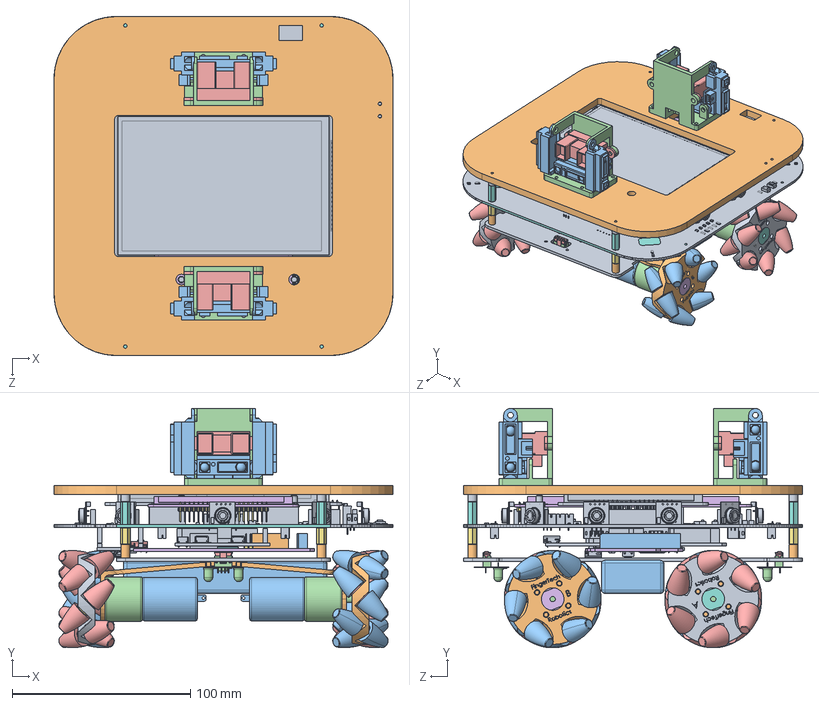
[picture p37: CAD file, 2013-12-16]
Mecânica/Robô_02.SLDASM
190.0 x 134.1 x 190.0 mm
Chassi
Suspensão x 2
Motor x 4
Motor_Redutor x 4
rubber roller x 24
steel pin x 12
Flat Washer Type A Narrow_AI_FW 0.125 x 24
Mecanum mount R2 x 2
Mecanum Hub A R2 x 2
Mecanum Hub Mirrored B R2 x 2
rubber roller_1 x 24
steel pin_1 x 12
Flat Washer Type A Narrow_AI_FW 0.125_1 x 24
Mecanum mount R2_1 x 2
PC-Standoff - 13mm - FF x 4
PC-Standoff - 13mm x 4
Espacador-Top x 4
Espacador-Bottom x 4
Bateria-Lipo1
Light Sensor Breakout x 2
PHR-4 x 2
Rescue-MainBoard
Proteção
Sharp_ir_sensor x 6
Ssuporte Sensor x 2
User Library-IR sensor-1 x 2

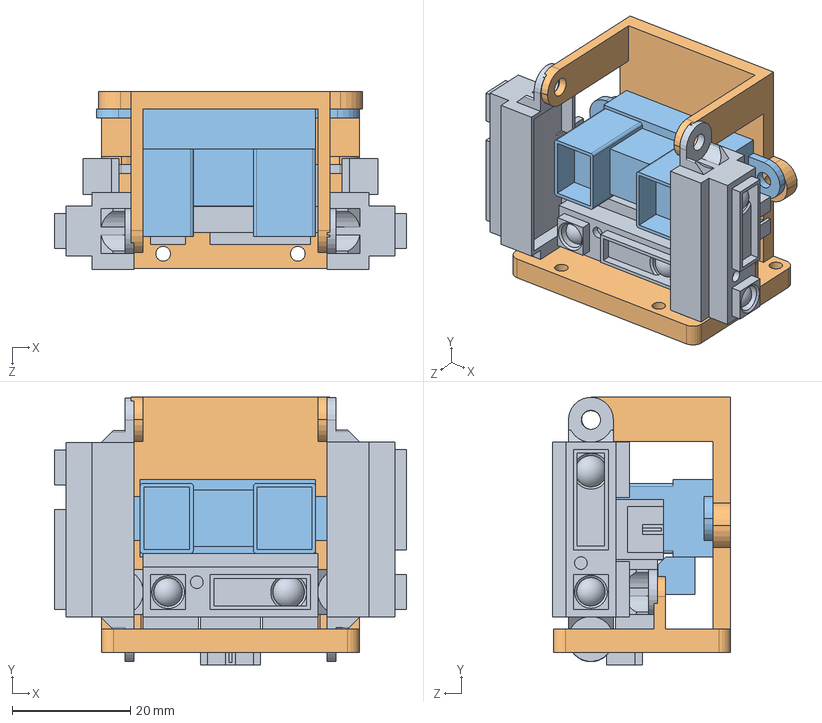
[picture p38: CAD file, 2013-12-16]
Mecânica/Montagens/IR Sensores (Cópia em conflito de ivan seidel 2013-03-28).SLDASM
59.6 x 45.3 x 30.2 mm
Sharp_ir_sensor x 3
Ssuporte Sensor
User Library-IR sensor-1

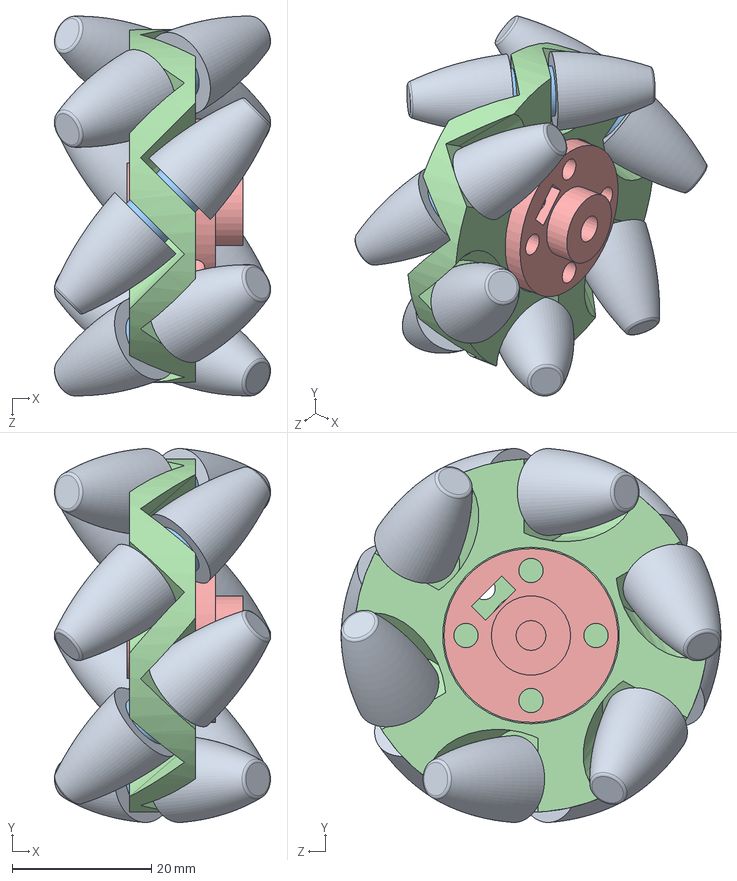
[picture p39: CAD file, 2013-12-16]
Mecânica/Peças/Mecanum Wheel A.SLDASM
31.1 x 53.8 x 54.6 mm
rubber roller x 12
steel pin x 6
Flat Washer Type A Narrow_AI_FW 0.125 x 12
Mecanum Hub A R2
Cilindro

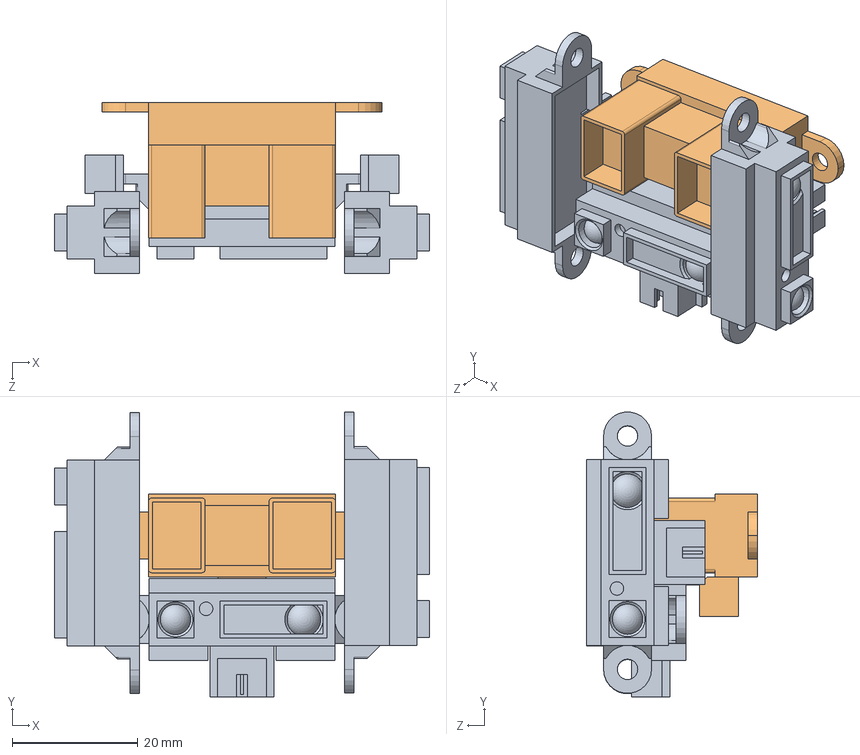
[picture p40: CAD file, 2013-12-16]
Mecânica/Montagens/IR Sensores.SLDASM
59.6 x 45.2 x 27.2 mm
Sharp_ir_sensor x 3
User Library-IR sensor-1

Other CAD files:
Mecânica/Cable_3-Robô_02.sldasm
Mecânica/Eletrônica/User Library-Sharp GP2Y0 Sensor.SLDASM
Mecânica/Montagens/Suspensão.SLDASM
Mecânica/Robô_01 (ivan seidel's conflicted copy 2013-04-02).SLDASM
Export/Board Outline.DWG
Export/Board Outline.DXF
Export/Chassi.STL
Export/Cilindro.STL
Export/Cubo.STL
Export/Mecanum Hub B R2.STL
Export/Protecao.Botao.STL
Export/Protecao.Leds.STL
Export/Proteção.DXF
Export/Ssuporte Sensor.STL
Export/Ssuporte Sensor2.STL
Export/Standoff - 7mm.stl
Export/Suporte.sensor.cor.STL
Export/Suspensao.STL
Export/Suspensao_plastico.STL
Export/molde.suspensao.DXF
Export/molde.suspensao.cobertura.DXF
Export/molde.suspensao2.DXF
Export/superior.DXF
Export/suporte Sensor.STL
Export/suporte.bateria.STL
Export/suporteSensor.STL
Mecânica/Ambiente/Rampa.SLDPRT
Mecânica/Arena/Suporte Arena.SLDPRT
Mecânica/Arena/Suporte Arena.STL
Mecânica/Botão.SLDPRT
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

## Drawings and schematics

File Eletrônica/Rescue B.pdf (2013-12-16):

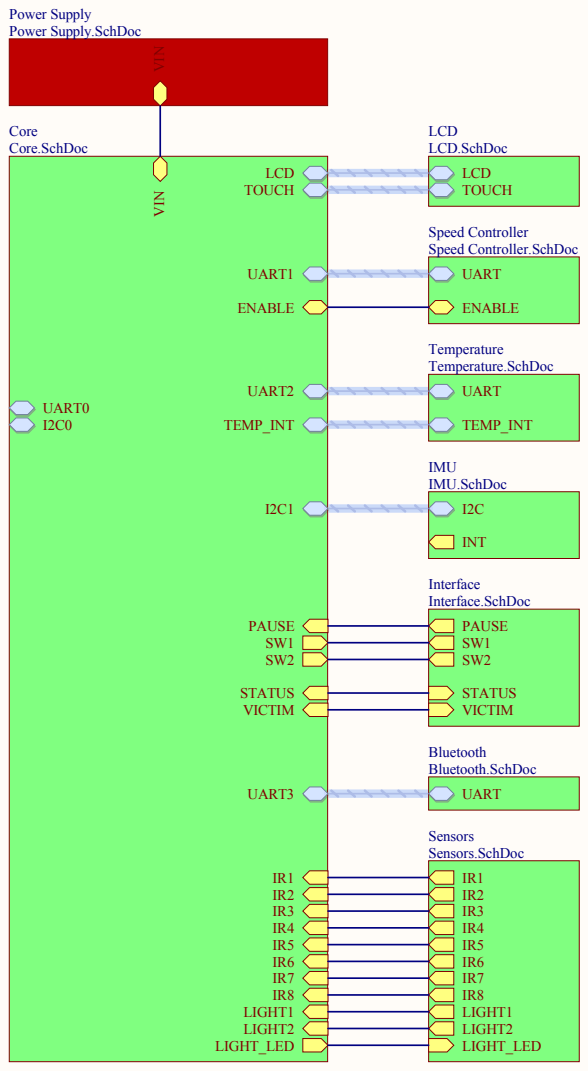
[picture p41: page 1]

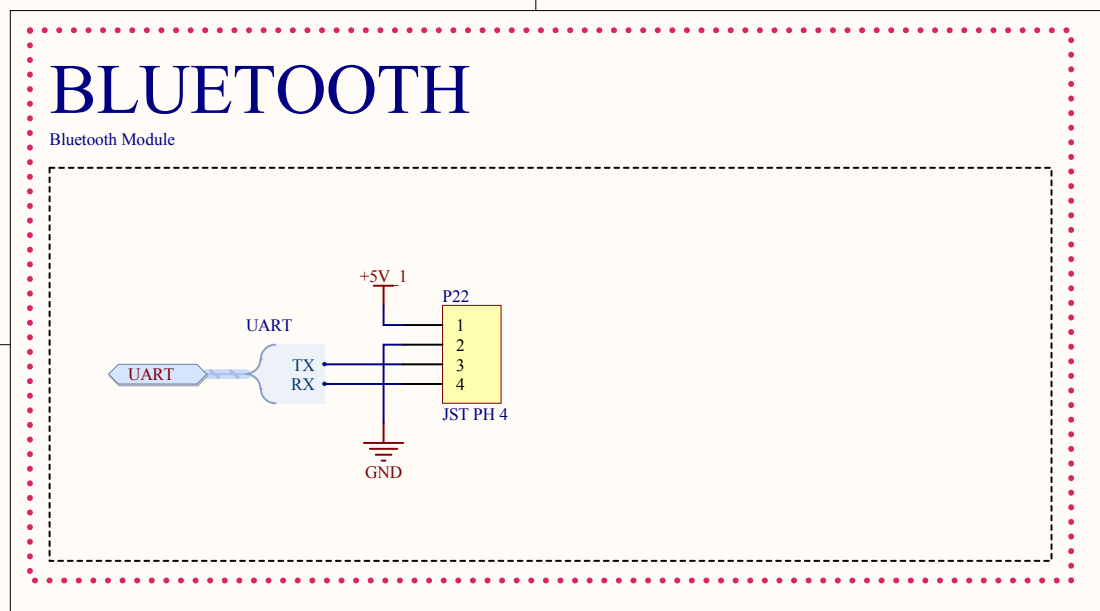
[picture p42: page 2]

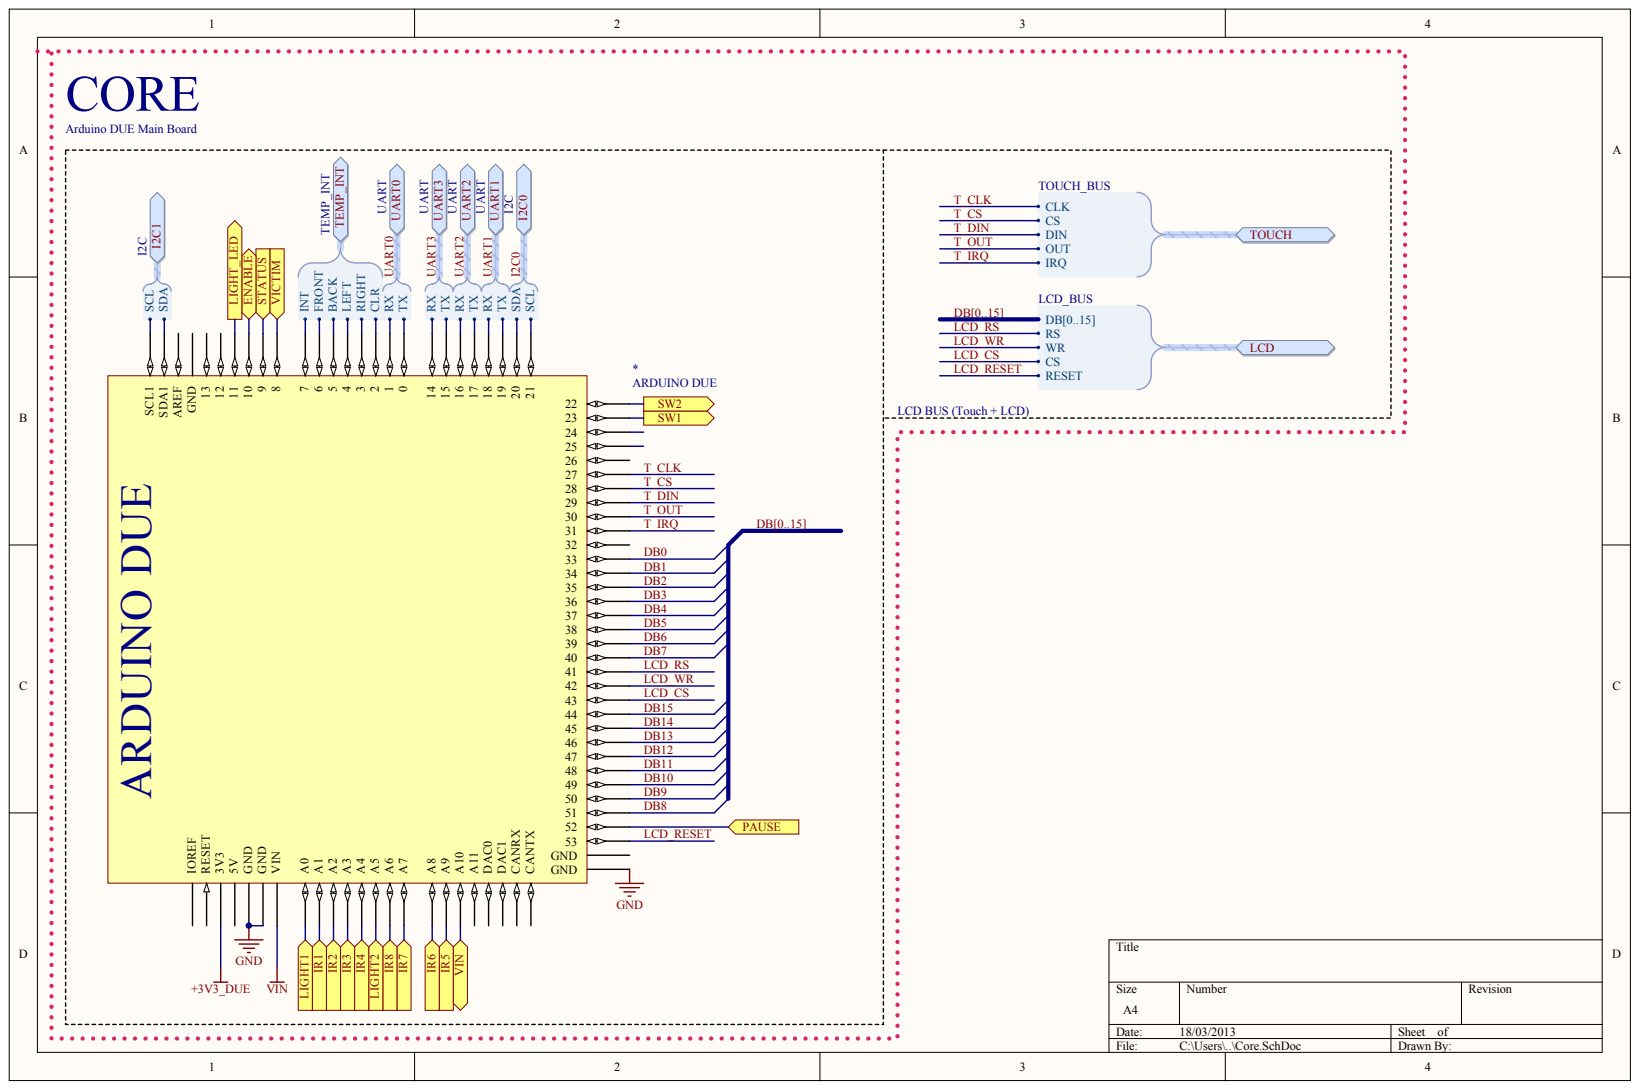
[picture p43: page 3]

CORE Arduino DUE Main Board

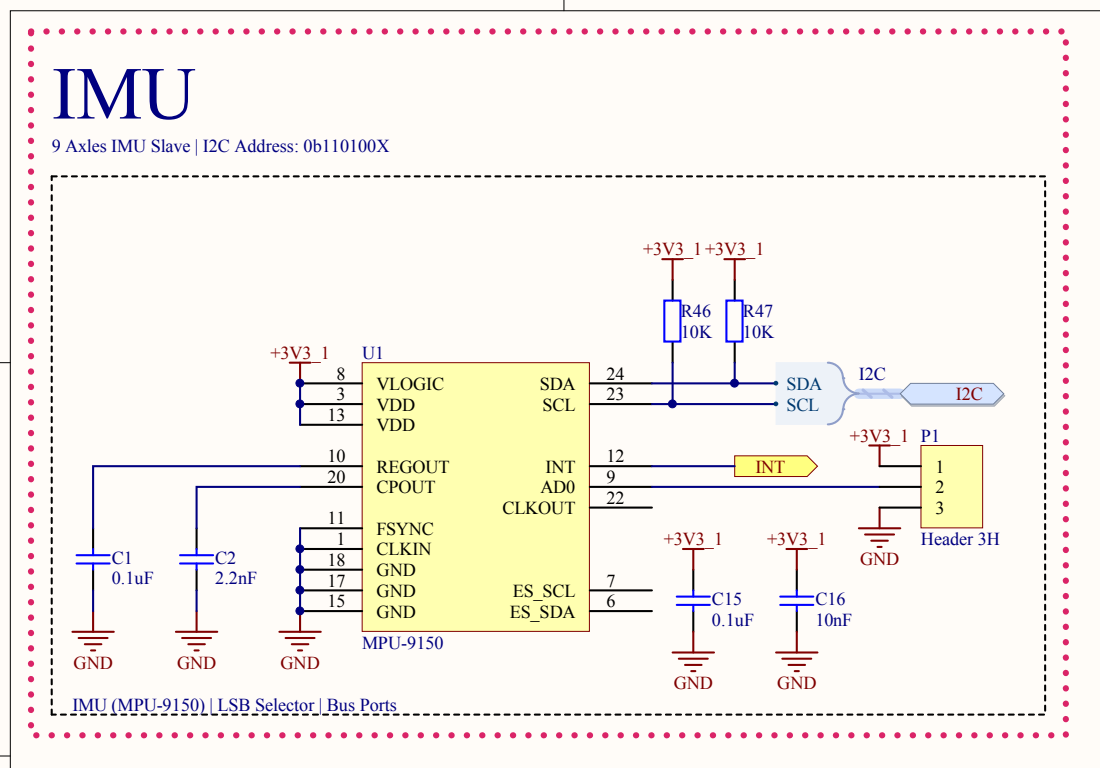
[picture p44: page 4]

U 9 Axles IMU Slave | I2C Address: 0b110100X

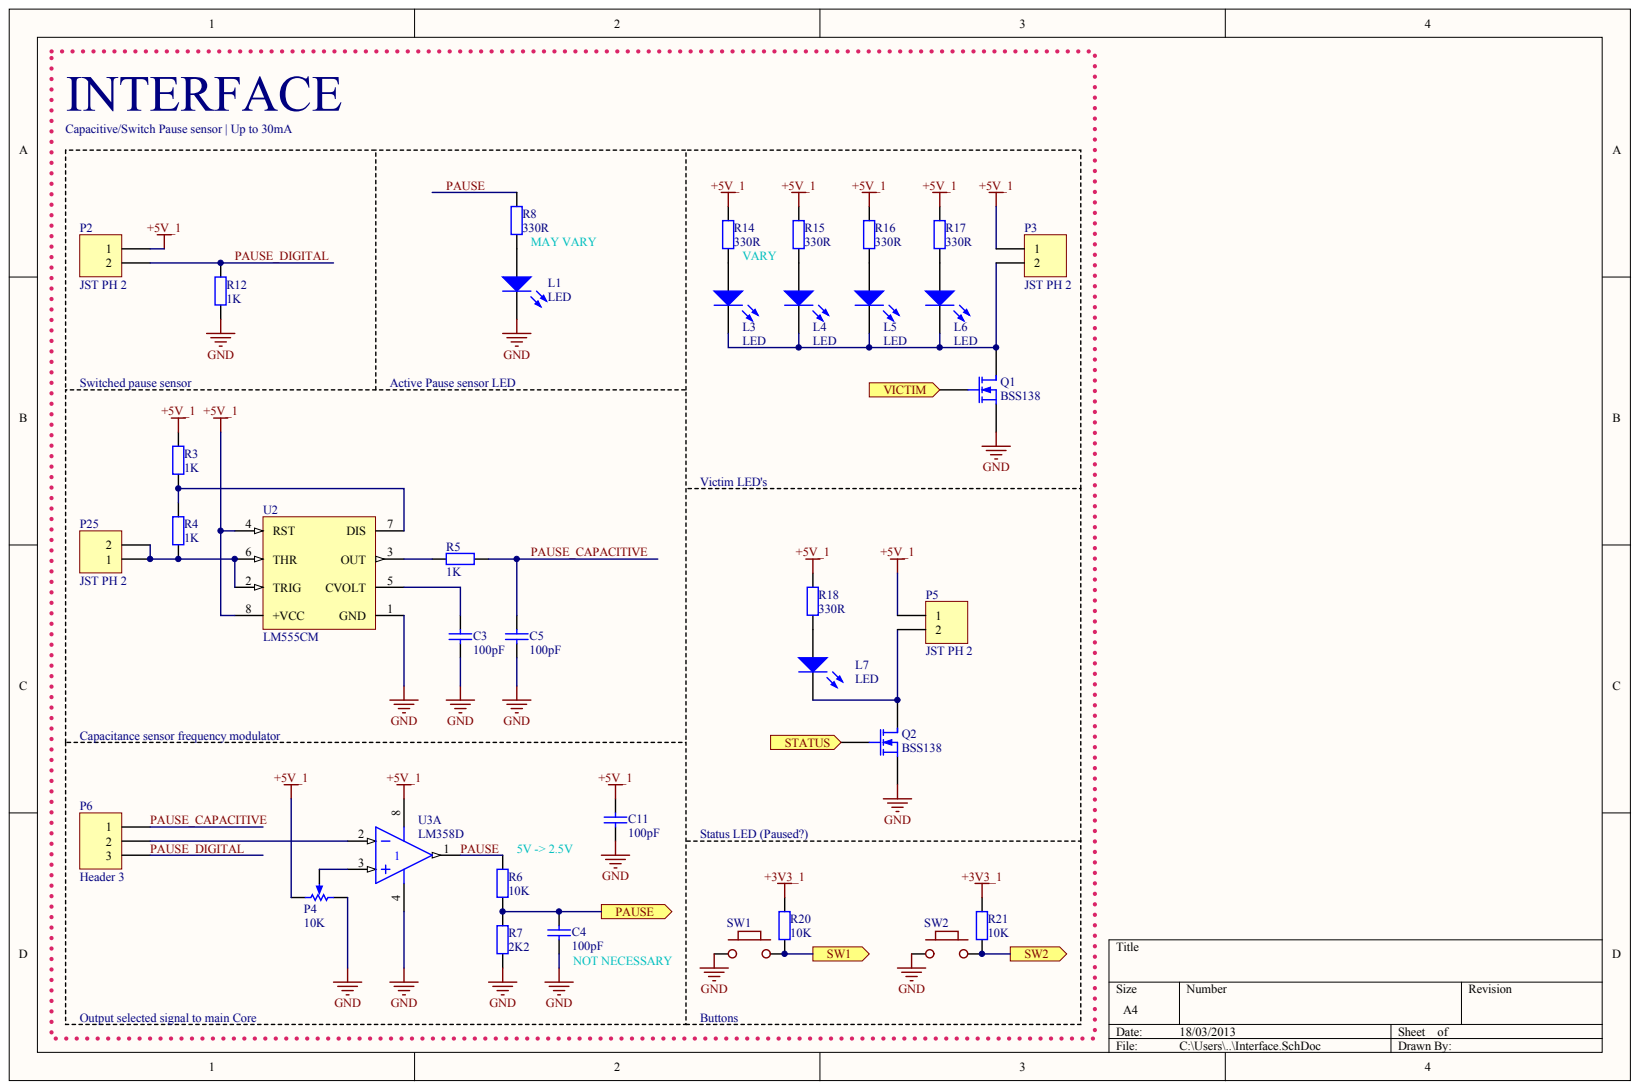
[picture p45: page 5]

Capacitive/Switch Pause sensor | Up to 30mA

Capacitance sensor frequency modulator

Output selected signal to main Core

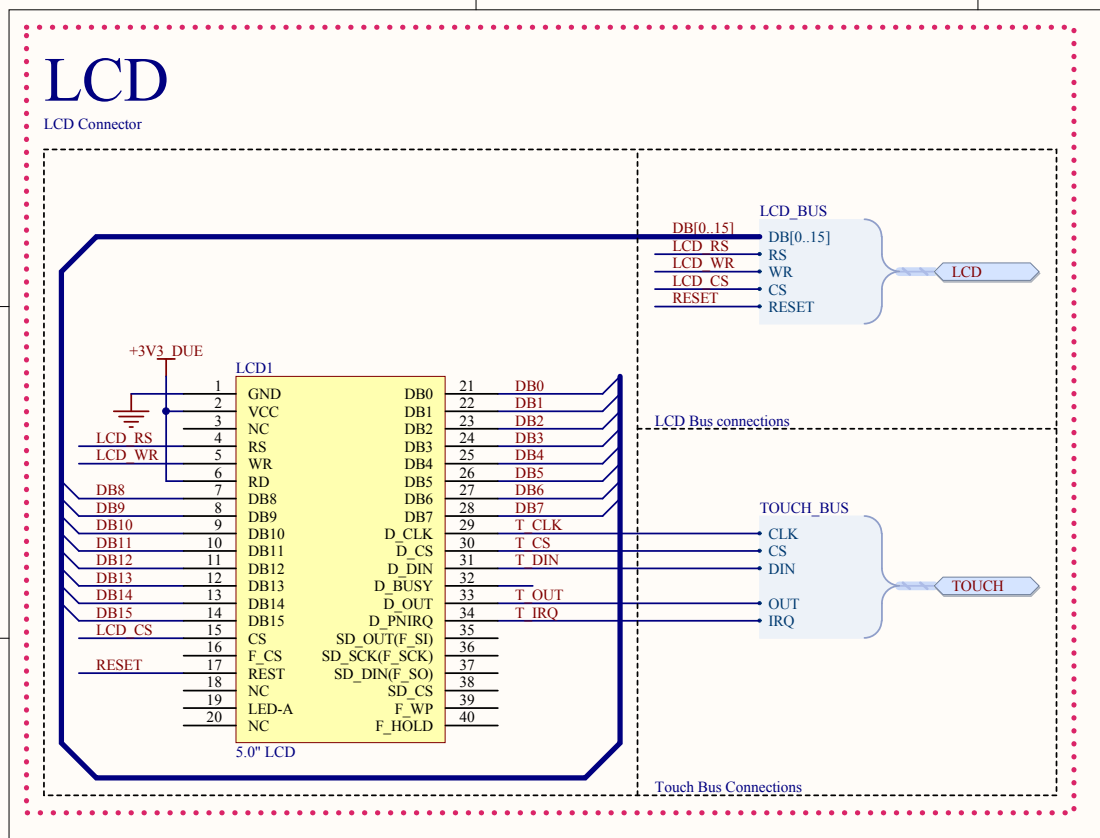
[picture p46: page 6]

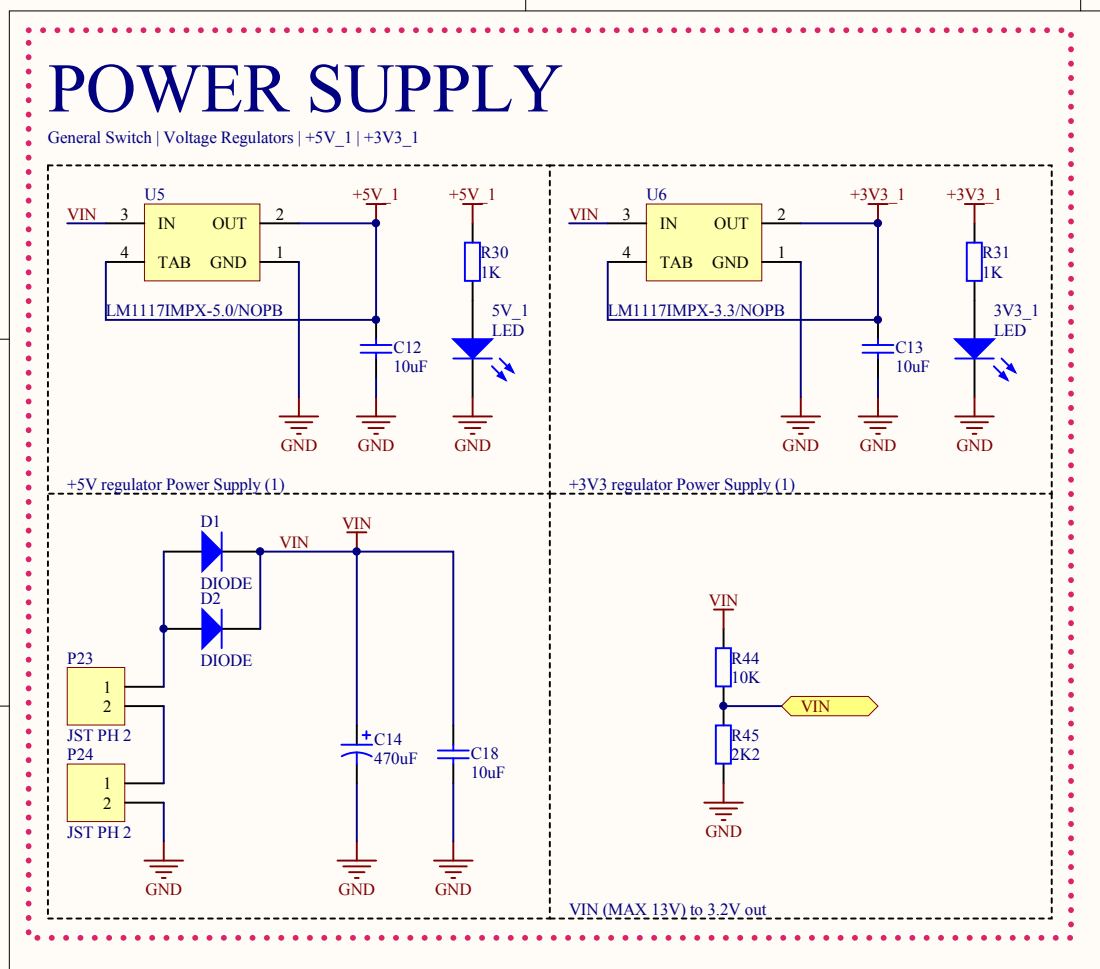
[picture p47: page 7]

POWER SUPPLY General Switch | Voltage Regulators | +5V_1 | +3V3_1

VIN (MAX 13V) to 3.2V out

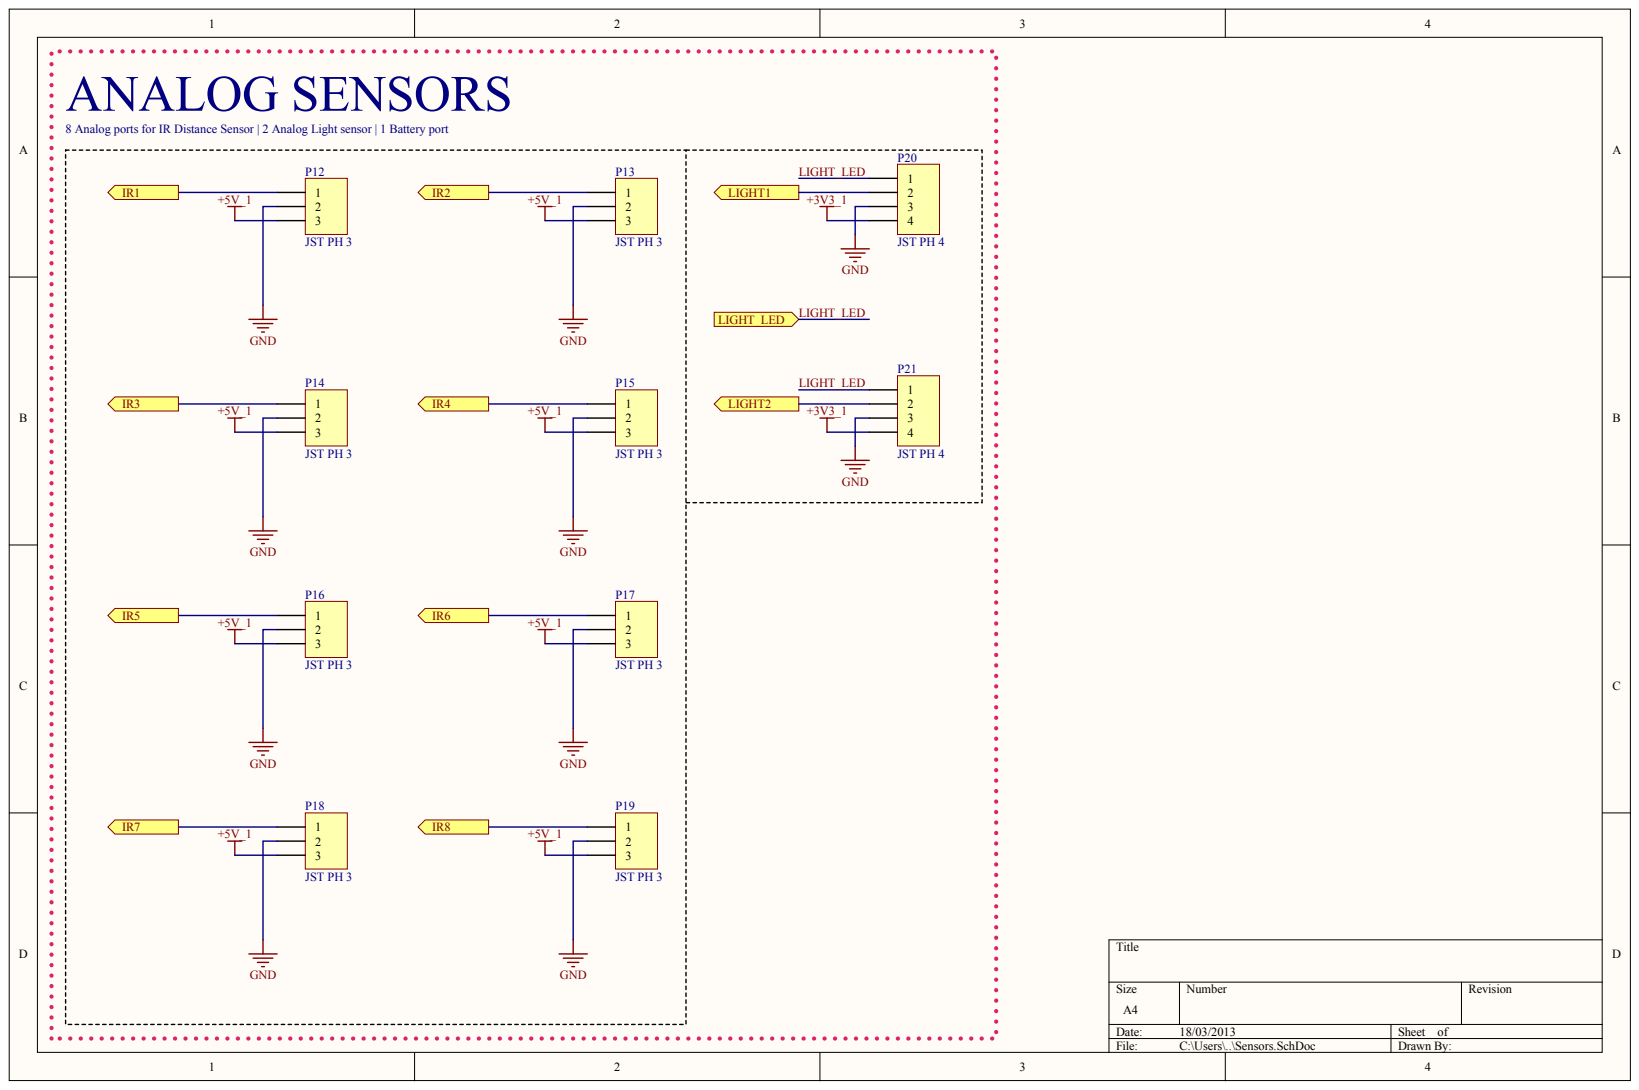
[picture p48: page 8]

8 Analog ports for IR Distance Sensor | 2 Analog Light sensor | 1 Battery port

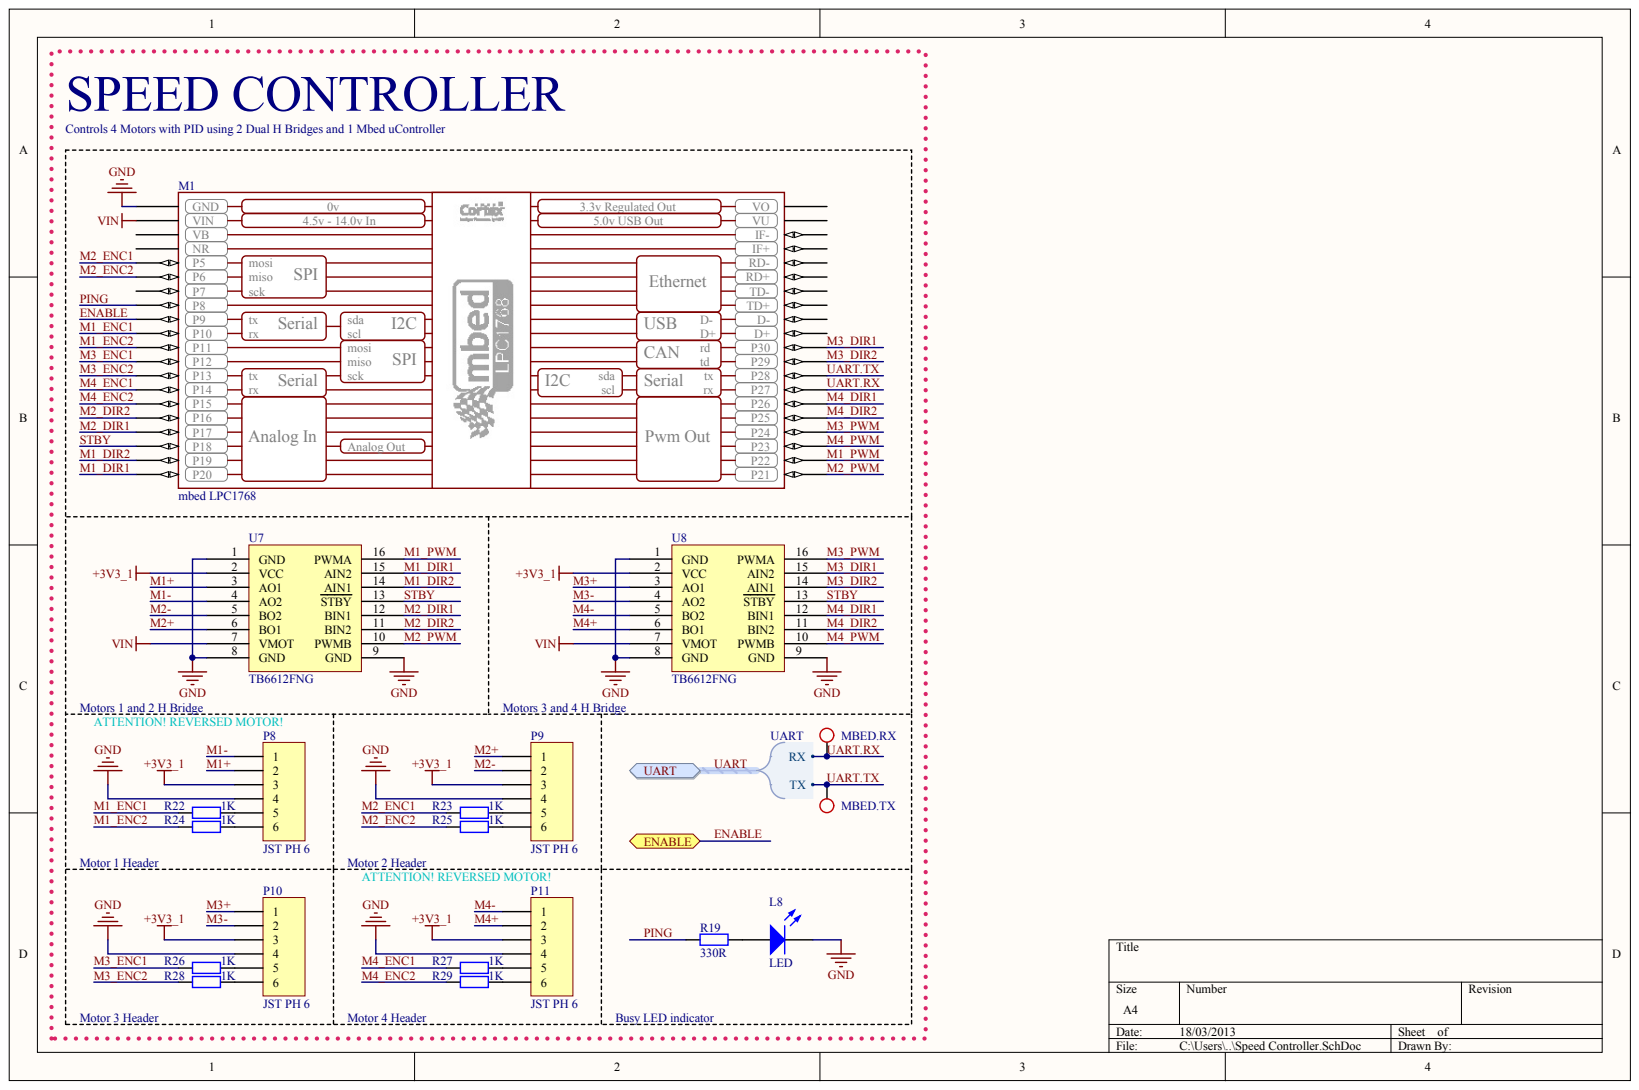
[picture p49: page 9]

SPEED CONTROLLER Controls 4 Motors with PID using 2 Dual H Bridges and 1 Mbed uController

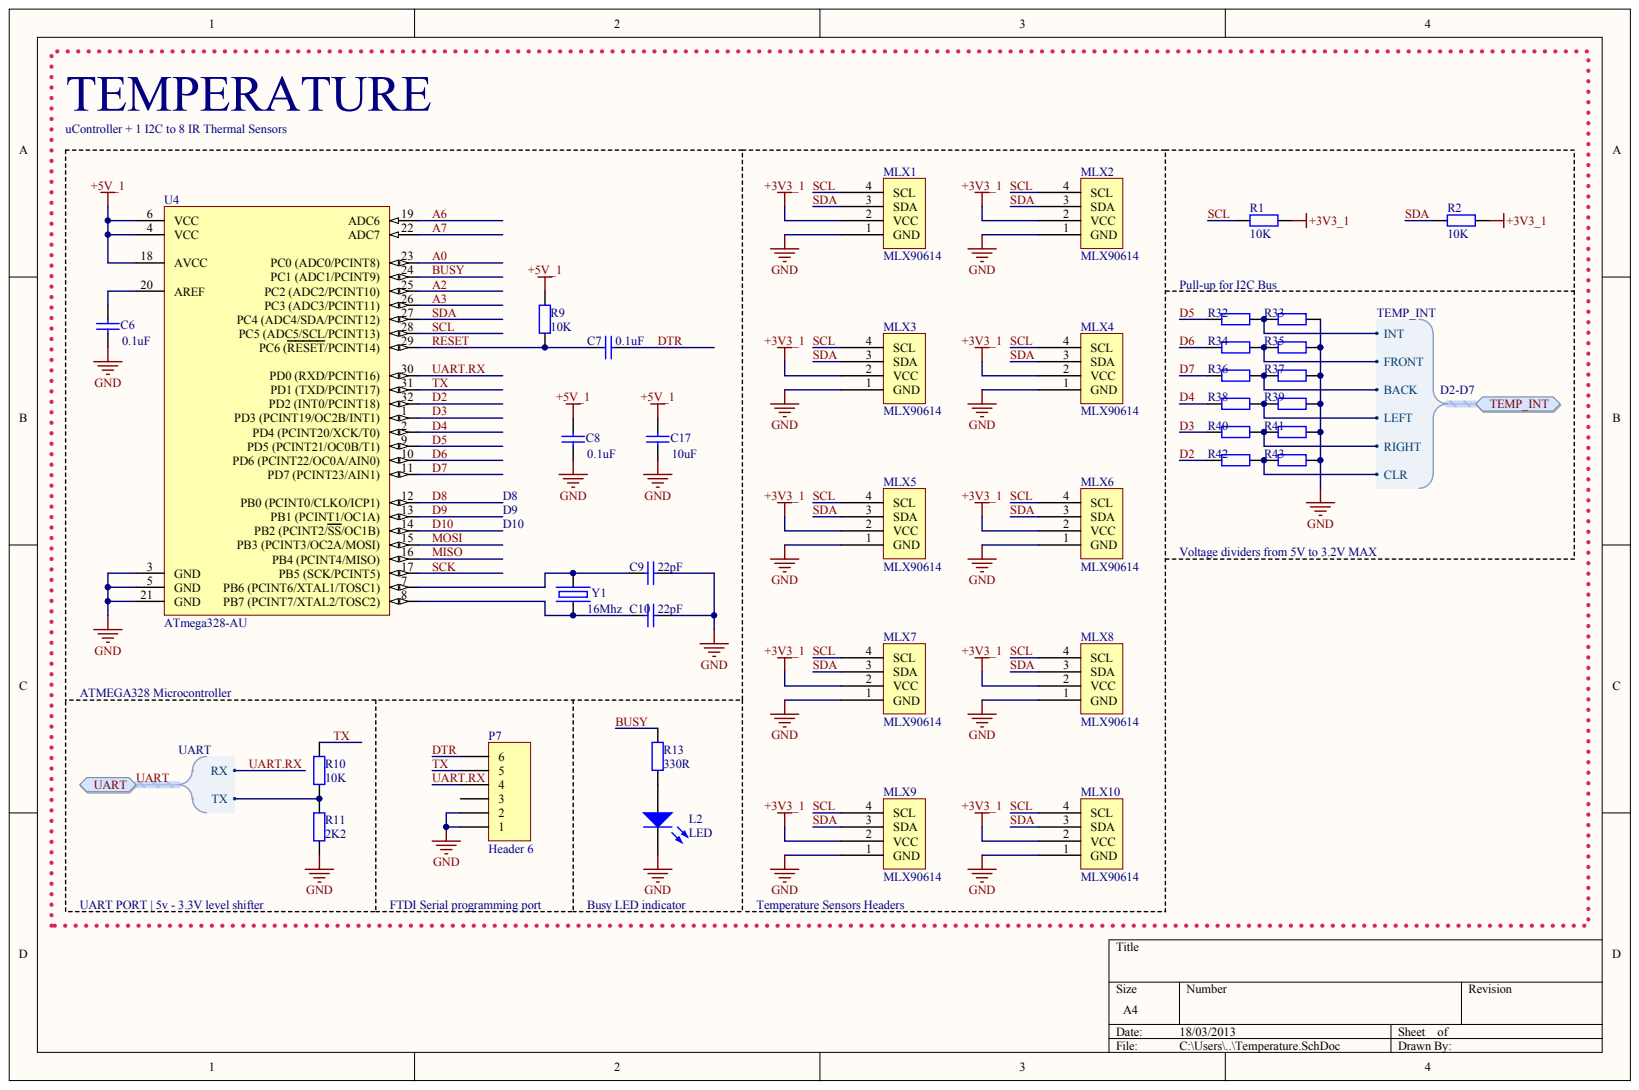
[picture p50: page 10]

GND 21 | Y1 8

UART PORT | 5v - 3.3V level shift

FTDI Serial programming port

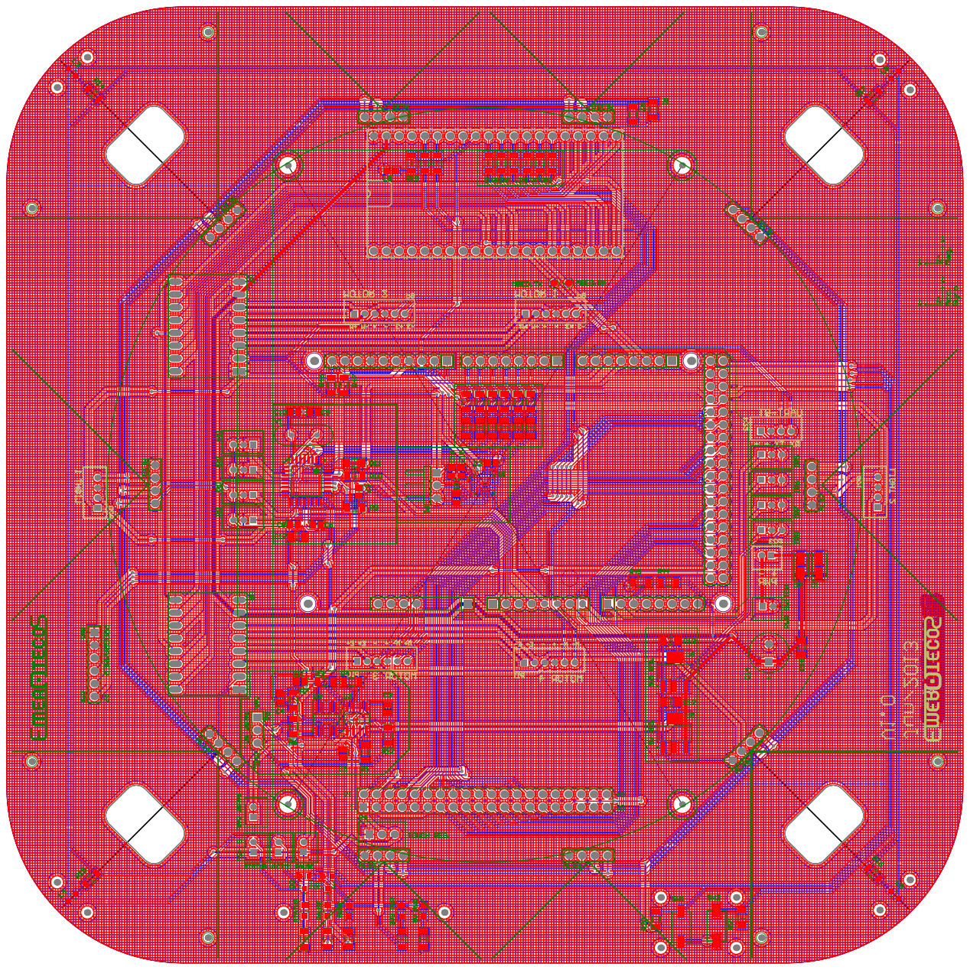
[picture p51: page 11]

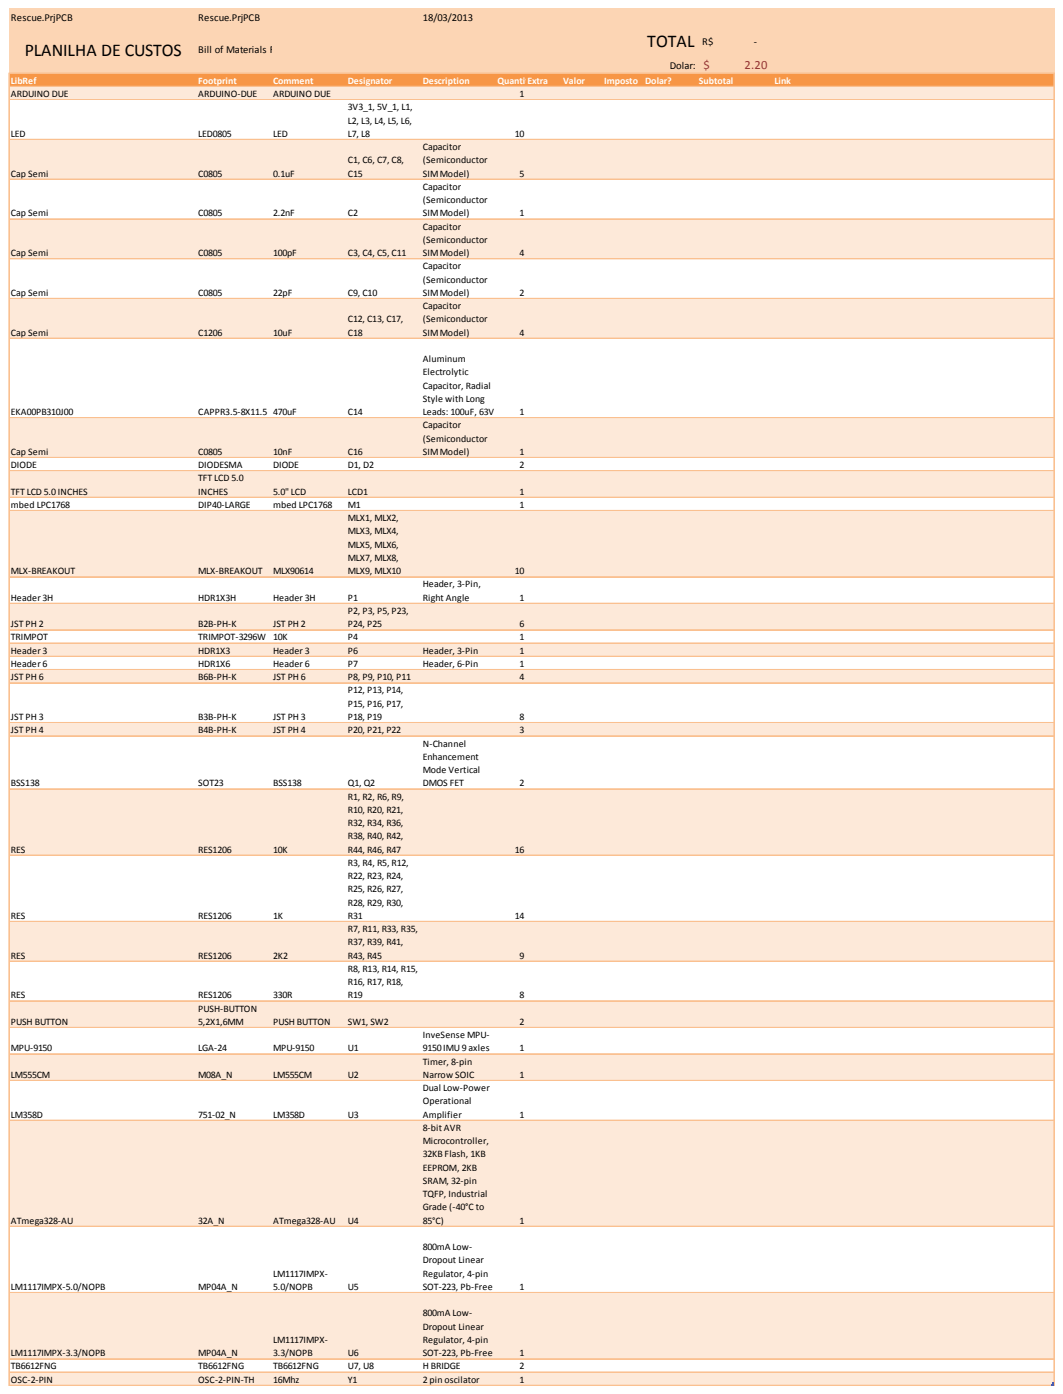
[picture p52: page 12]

PLANILHA DE CUSTOS Bill of Materials F

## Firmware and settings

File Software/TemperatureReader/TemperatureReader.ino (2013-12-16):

// System Includes
#include <inttypes.h>
#include <math.h>

// Custom Includes
#include <EEPROM.h>
#include <I2Cmaster.h>
#include <MLX90614.h>

// Custom board Definitions
const int LED = A1;

/*
    Data communication definitions
*/
#define USART_SPEED             9600

#define CMD_READ_ALL            'r'
#define CMD_SETUP_ALL_SENSORS   's'
#define CMD_LIST_CONNECTIONS    'l'
#define CMD_SET_DEFAULT_VALUES  'd'
#define CMD_QUIT                '0'
#define CMD_CHECK_ALIVE         'a'
#define CMD_PERFORM_READ        'p'

// Raw Commands
#define CMD_SET_MIN_DEVIATION   'm' // Should be followed by a single byte
                                    // containing the DEVIATION*50
                                    // unsigned uint8_t type

#define CMD_START_BYTE          0xFF
#define CMD_SIZE                14  // Size of packet sent from ATMEGA328

#define DEFAULT_MIN_DEVIATION   1.0
#define DEVIATION_PRESCALE      20
#define VECTOR_PRESCALE         2
#define VECTOR_ZERO             64
#define TEMPERATURE_PRESCALE    2


/*
   Useful functions, just for easy coding...
*/
void workStart(){
    digitalWrite(LED, HIGH);
}

void workDone(){
    digitalWrite(LED, LOW);
}

void clearArray(int* array, int size, int val = 0){
    for(int i = 0; i < size; i++)
        array[i] = val;
}

float standard_deviation(float data[], int n)
{
    float mean=0.0, sum_deviation=0.0;
    int i;
    for(i=0; i<n;++i)
    {
        mean+=data[i];
    }
    mean=mean/n;
    for(i=0; i<n;++i)
    sum_deviation+=(data[i]-mean)*(data[i]-mean);
    return sqrt(sum_deviation/n);           
}

// Configurations on EEPROM
#define MAX_SENSORS         10
#define ADR_SENSORS_START   0x32
#define ADR_MIN_DEVIATION   0x60

// Get all sensors written on EEPROM.
// Sets the addresses to the pointer array
void readSensors(int* addresses){
    for(int i = 0; i < MAX_SENSORS; i++){
        addresses[i] = EEPROM.read(ADR_SENSORS_START+i);
    }
}

// Saves a sensors.
// positon = -1: saves on the last positon possible. if full, override last one.
void setSensor(int address, int position = 0){
    position = (position < 0? 0: position);
    position = (position > MAX_SENSORS? MAX_SENSORS: position);

    EEPROM.write(ADR_SENSORS_START+position, address);
}

double readMinDeviation(){
    return EEPROM.read(ADR_MIN_DEVIATION)/(DEVIATION_PRESCALE*1.0);
}

void setMinDeviation(uint8_t val){
    EEPROM.write(ADR_MIN_DEVIATION, val);
}

void setMinDeviation(double val){
    setMinDeviation((uint8_t)(val*DEVIATION_PRESCALE));
}

void setDefaultValues(){
    // Set default values for Temperatures Addresses
    for(int i = 0; i < 10; i++)
        setSensor(i+1, i);

    // Set Default Deviation
    setMinDeviation(DEFAULT_MIN_DEVIATION);
}

/*
    Local data storage for sensors and configs
*/

// MLX90644 communication objects, used to read and check sensors
MLX90614 sensors[MAX_SENSORS];

// Buffer to store last sensors measurements (easy and fast access)
float _temp[MAX_SENSORS] = {NULL};

float _minDeviation = 0.0;

// Keeps the sensor angles for current configuration. Angles are in radians
float _tempAngles[MAX_SENSORS] = {
    0.0,                // 0
    PI/4.0,             // 45
    1.309,              // 90  // 45+30  = 75
    1.83259,            // 90  // 135-30 = 105
    PI - HALF_PI,       // 135
    PI,                 // 180
    PI + PI/4.0,        // 225
    4.4506,             // 270 // 225+30 = 255
    4.97418,            // 270 // 315-30 = 285
    TWO_PI - HALF_PI,   // 315
};

float _tempWeights[MAX_SENSORS] = {
    1,                  // 0
    1,                  // 45
    0.8,                // 90
    0.8,                // 90
    1,                  // 135
    1,                  // 180
    1,                  // 225
    0.8,                // 270
    0.8,                // 270
    1,                  // 315
};

void loadSensors(){
    int sensorsAdr[MAX_SENSORS] = {};
    readSensors(sensorsAdr);

    for(int i = 0; i < MAX_SENSORS; i++){
        sensors[i] = MLX90614(sensorsAdr[i]);
    }

    _minDeviation = readMinDeviation();
}

/*
    Command Functions
*/

void listAllSensors(){
    int found[10];
    int total = MLX90614::scanAll(1, 127, 10, found);

    if(total>0){
        Serial.print("\t");
        for(int i = 0; i < total; i++){
            Serial.print("[");
            Serial.print(found[i]);
            Serial.print("] ");
        }
        Serial.println("");
    }
}

void listConnectionStatus(){

    int sensorsAdr[MAX_SENSORS] = {};
    bool sensorsStatus[MAX_SENSORS] = {};
    readSensors(sensorsAdr);

    for(int i = 0; i < MAX_SENSORS; i++){
        sensorsStatus[i] = MLX90614::scan(sensorsAdr[i], sensorsAdr[i]) > 0;
    }

    Serial.print("\t");
    bool con;
    int adr;
    for(int i = 0; i < MAX_SENSORS; i++){
        adr = sensorsAdr[i];
        con = sensorsStatus[i];

        if(adr == 0x00 || adr == 0xFF){
            Serial.print(" [----]  ");
        }else{
            if(con)Serial.print("<[");
            else Serial.print(" [");

            if(adr < 16)Serial.print("0x0");
            else Serial.print("0x");

            Serial.print(adr, HEX);
            
            if(con)Serial.print("]> ");
            else Serial.print("]  ");
        }
    }
    Serial.println("");
}

void setupAllSensors(){
    Serial.println("\t#Please, to change one sensor address, leave ONLY him connected");

    int found[10] = {0,0,0,0,0,0,0,0,0,0};
    int total_found = 0, last_total = 0;
   
    int filter;
    last_total = 0;
    while(true){
        total_found = MLX90614::scanAll(1, 127, 10, found);

        if(Serial.available()){
            char c = Serial.read();
            int pos = c - '0'+1;
            if(pos > 10 || pos <= 0){
                Serial.println("\t#Setup Ended: Wrong input");
                return;
            }else{

                Serial.println("\t#Changing address...");
                MLX90614 _mlx = MLX90614(found[0]);
                if(_mlx.changeAddress(pos)){
                    setSensor(pos, pos-1);
                    Serial.println("\n#Change complete! Unplug and plug to have effect.");
                    listConnectionStatus();
                }else{
                    Serial.println("\n#ERROR! Could not change address.");
                }

                Serial.print("\t#New Address: ");
                Serial.println(pos, HEX);

                Serial.println("\t#Unplug and plug to have affect!");
            }
        }

        if(total_found != last_total){
            if(filter <= 1){
                filter ++;
            }
            Serial.print("\t#Devices connected: ");
            Serial.println(total_found);
            last_total = total_found;
            listAllSensors();
        }

        last_total = total_found;
    }
}

// Prints a bar graph
void printBarGraph(float min, float max, int ysize, float vals[], int n){
    /*for(int k = 0; k < 30; k++){
        Serial.print("\n");
    }*/
    // Serial.println("-----------------------------------------------");

    float rel = (max-min)/ysize;

    for(int i = 0; i < n; i++){
        for(int x = 0; x < ysize; x++){
            if((vals[i]-min) >= x*rel){
                Serial.print("=");
            }else{
                break;
            }
        }
        Serial.print("| ");
        Serial.print(vals[i]);
        Serial.print("\n");
    }
    // Serial.println("-----------------------------------------------");
}

/*
    MAIN CODE
*/

#define UPDATE_INTERVAL     50

char c;
bool _sendData = false;
long _err = 0;
long lastRun = 0;

float deviation;
float vX, vY, angle;


void setup(){
    pinMode(LED, OUTPUT);

    Serial.begin(USART_SPEED);
    Serial.println("$Initializing...");
    
    MLX90614::init();
    loadSensors();

    Serial.println("$Ready!");
}

#define MSK         0b01111111
uint8_t buff[64];

void loop(){
    // Check for messasges on Serial, if some, enter terminal mode
    if(Serial.available()){
        workStart();
    
        int c = Serial.read();
        if(c == CMD_PERFORM_READ){
            _sendData = true;
        }if(c == CMD_READ_ALL){
            Serial.println("$ ListAll");
            listAllSensors();
        }else if(c == CMD_SETUP_ALL_SENSORS){
            Serial.println("$ Setup");
            setupAllSensors();
            loadSensors();
        }else if(c == CMD_LIST_CONNECTIONS){
            Serial.println("$ ActCon");
            listConnectionStatus();
        }else if(c == CMD_SET_DEFAULT_VALUES){
            Serial.println("$ ResetDef");
            setDefaultValues();
            loadSensors();
        }else if(c == CMD_QUIT){
        }else if(c == CMD_CHECK_ALIVE){
            Serial.write(0xFF);
        }else if(c == CMD_SET_MIN_DEVIATION){
            delay(1);
            if(Serial.available() > 0)
                setMinDeviation((uint8_t)Serial.read());
            Serial.write((uint8_t)(readMinDeviation()*DEVIATION_PRESCALE));
            loadSensors();
        }else{
            Serial.println("$ CMDNOTFOUND");
        }
        Serial.flush();
        workDone();
    }

    // Check if should execute sensor data processing
    workStart();
    
    // Start of real work
    // Reads all sensors
    for(int i = 0; i<MAX_SENSORS; i++){
        _temp[i] = sensors[i].read();

        if(_temp[i] < 0){ // Correct communication errors
            _err++;
            _temp[i] = 0;
        }
    }

    // Fix zeroes (mistakes on Communication)
    // TODO

    // Find average, minimum and maximum
    float min = 999, max = 0, avg;

    for(int i = 0; i<MAX_SENSORS; i++){
        min = (_temp[i] < min? _temp[i]: min);
        max = (_temp[i] > max? _temp[i]: max);
        avg += _temp[i];
    }
    avg = avg/MAX_SENSORS;

    // Calculate Mean and Standard Deviation
    deviation = standard_deviation(_temp, MAX_SENSORS);

    // Calculate vector angle for measurements
    vX = 0.0;
    vY = 0.0;

    for(int i = 0; i < MAX_SENSORS; i++){
        vX += (_temp[i]*_tempWeights[i]-min)*sin(_tempAngles[i]);
        vY += (_temp[i]*_tempWeights[i]-min)*cos(_tempAngles[i]);
    }

    angle = atan2(vX, vY)*180.0/PI;



    if(millis() - lastRun >= UPDATE_INTERVAL){
        lastRun = millis();

        /*
            Potocol definitions
            
            MSK = 0b01111111

            Byte 0: 0b1000000 // Start Byte
            Byte 1: Deviation | MSK
            Byte 2: VecX      | MSK
            Byte 3: VecY      | MSK

            Byte 4..13: SensorValX | MSK

            // Interruptions should be done as follows:

            Is Reset Flag enabled?
                Disable ALL outputs

            Is there victim?
                Set Direction flags (RIGHT, LEFT, FRONT, BACK)
                Output high on Interrupt pin


        */
        buff[0] = CMD_START_BYTE;
        buff[1] = (uint8_t)(deviation*DEVIATION_PRESCALE) & MSK;
        buff[2] = ((uint8_t)(vX*VECTOR_PRESCALE) + VECTOR_ZERO) & MSK;
        buff[3] = ((uint8_t)(vY*VECTOR_PRESCALE) + VECTOR_ZERO) & MSK;

        for(int i = 0; i < 10; i++)
            buff[i+4] = (uint8_t)(_temp[i]*TEMPERATURE_PRESCALE) & MSK;

        Serial.write(buff, 14);

        _sendData = false;
    }

    TWCR = 0;
    workDone();
    /*Serial.print("-------------\n");
    for(int i = 0; i < 14; i++){
        Serial.println(buff[i]);
    }*/
    /*Serial.print(deviation);
    Serial.print("\t");
    Serial.print(vX);
    Serial.print("\t");
    Serial.print(vY);
    Serial.print("\t");
    Serial.print(sqrt(vX*vX + vY*vY));
    Serial.print("\t");
    Serial.println(angle);*/

    // Output data for debbug
    /*printBarGraph(min, max, 50, _temp, MAX_SENSORS);
    Serial.print("DEVIATION: ");
    Serial.println(deviation);

    Serial.print("VECTOR:\tx=");
    Serial.print(vX);
    Serial.print("\ty=");
    Serial.println(vY);

    Serial.print("ANGLE: ");
    Serial.println(angle);*/

    /*Serial.print(angle);
    Serial.print("\t");
    Serial.println(deviation);*/

    // Reset I2C bus state
}

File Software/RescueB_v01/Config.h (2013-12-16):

#include <Arduino.h>
#include <DueTimer.h>

/*
	ROBOT GENERAL CONFIGURATION
*/

// Timers usage definition, to avoid conflicts
#define TIMER_THREAD1	Timer3		// Timer that will trigger threads on ArduinOS
#define TIMER_TCH		Timer4		// Used for LCD hit tests while moving
#define TIMER_LED		Timer5		// Blinking led, to show that "I'm alive!"


// User Interface (LED's, Buzzer...)
#define pLED_STATUS		9
#define pLED_VICTIM		8
#define pBTN_PAUSE		DAC0
#define pBTN_SW1		23
#define pBTN_SW2		22

// Buzzer configuration
#define pBUZER			12
#define TIME_BEEP		20
#define TIME_BEEP_H		1 			
#define TIME_BEEP_L		200			

// PC (Just for debugging)
#define PC_USART		Serial
#define PC				Serial 		// To simplify

// Bluetooth
#define BLUETOOTH_USART	Serial3
#define BLUETOOTH		Serial3

// Motor Driver Controller
#define DRIVER_USART	Serial1
#define pDRIVER_ENABLE	10

// CO-PROCESSOR (ATMEGA328) with Temperature sensors
#define VICTIM_USART	Serial2
#define pTMP_INT		7
#define pTMP_FRONT		6
#define pTMP_BACK		5
#define pTMP_LEFT		4
#define pTMP_RIGHT		3
#define pTMP_CLR		2

// LCD
// DB0-DB7:  33-40
// DB8-DB15: 51-44
#define pLCD_RS			41
#define pLCD_WR			42
#define pLCD_CS			43
#define pLCD_RESET		53
#define pLCD_LED		DAC1

#define LCDWidth		799
#define	LCDHeight		479

// TOUCH
#define pTCH_CLK		27
#define pTCH_CS			28
#define pTCH_DIN		29
#define pTCH_OUT		30
#define pTCH_IRQ		31

// IMU
#define IMU_WIRE		Wire1
#define pIMU_SDA		SDA1
#define pIMU_SCL		SCL1
#define pIMU_IRQ		32

// SD Card
// Uses SPI pins, no need for definition
#define pSD_CS			52

// Battery voltage
#define pVIN			A11
#define VOLTAGE_USB		110			// In raw units of analogRead()
#define VOLTAGE_LOW		6.4
#define VOLTAGE_HIGH	8.2

// Light Sensors
#define pLIGHT_IN1		A0
#define pLIGHT_IN2		A5
#define pLIGHT_LED		11

int pLIGHT_IN[] = {
	pLIGHT_IN1,
	pLIGHT_IN2
};

// IR Distance Sensor
#define IR_Short		0
#define IR_Medium		1
#define IR_Long			2

#define pIR_IN1			A1
#define pIR_IN2			A2
#define pIR_IN3			A3
#define pIR_IN4			A4
#define pIR_IN5			A10
#define pIR_IN6			A9
#define pIR_IN7			A7
#define pIR_IN8			A6

int pIR_IN[] = {
	pIR_IN1,
	pIR_IN2,
	pIR_IN3,
	pIR_IN4,
	pIR_IN5,
	pIR_IN6,
	pIR_IN7,
	pIR_IN8,
};

int IR_TYPE[] = {
	IR_Medium,
	IR_Short,
	IR_Long,
	IR_Medium,
	IR_Medium,
	IR_Long,
	IR_Short,
	IR_Medium
};

/*
	LCD Schemes
*/
#define cRectFill		200,200,200
#define cTextNeutral	30,30,30
#define cGUITopBarFill	255,255,255

#define fTextBig		OCR_A_Extended_M
#define fTextSmall		SmallFont
#define fNumBig			SevenSegNumFont

/*
	ArduinOS Configuration
*/
#define osRETURN_MIN_TIME	100		// Minimum time between clicks on return Btn
									// to debounce sensor. (in Milliseconds)
									
#define UPDATE_GUI_INTERVAL	2000	// Time to update GUI (constantly)
									// Also compute the remaining battery

#define fGUI_USB			9

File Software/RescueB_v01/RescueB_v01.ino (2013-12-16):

// ------------- ECONOMIZE MEMORY -------------
// Disable Definitions (Make code lighter)

// #define DISABLE_ZYGOTE	1

// #define DISABLE_VICTIM	1
// #define DISABLE_SENSORS	1
// #define DISABLE_IMU		1
// #define DISABLE_MOTION	1
// #define DISABLE_LCD		1 	// Also disables Touch
								// Disabling LCD will cause WEIRD things
//#define DISABLE_CATABRIGA	1
// #define DISABLE_PROGRAM1	1
// --------------------------------------------


// Motors incluedes
#ifndef DISABLE_MOTION
	#include "MoveController.h"
	#include "MbedDriver.h"
#endif

// General peripheral includes
#include <DueTimer.h>

#include <ArdUI.h>
#include <View.h>

// LCD stuff
#ifndef DISABLE_LCD
	#include <UTouch.h>
	#include <UTFT.h>
#endif

// #include "Util.h"

// IMU includes
#ifndef DISABLE_IMU
	#include "Wire.h"
	#include "I2Cdev.h"
	#include "dmpMPU9150.h"
	#include "sensors/IMUSensor.h"
#endif

#include <Utilities.h>
#include "BFS.h"

// VICTIM includes
#ifndef DISABLE_VICTIM
	#include "VictimChecker.h"
#endif

#ifndef DISABLE_ZYGOTE
	#include <LinkedList.h>
#endif

// Analog Sensors
#include <sensors/AnalogIn.h>
#include <sensors/DigitalOut.h>
#include <sensors/SharpShort.h>
#include <sensors/SharpMedium.h>
#include <sensors/SharpLong.h>
#include <sensors/CompoundDistanceSensor.h>

// Operational System
#include <Thread.h>
#include <ArduinOS.h> 
#include <views/Button.h>
#include <views/CheckBox.h>
#include <views/ProgressBar.h>
#include <views/SeekBar.h>
#include <views/TextView.h>
#include <views/DrawableLine.h>
#include <views/AngleView.h>
#include <views/LinearLayout.h>
#include <views/GraphicView.h>
#include <Gaussian.h>

// Rescue Classes (Map, Cell, Wall...)
#include "Rescue.h"
#include "MapView.h"
#include "AngleEstimator.h"
#include "DistanceEstimator.h"
#include "PoseEstimator.h"
#include "GaussianAverage.h"
#include "MazeWalker.h"

// Basic robot definitions
#include "Config.h"
#include "Robot.h"

// Activity includes
#include "MainActivity.h"
#include "TestIMUActivity.h"
#include "TestVictimActivity.h"
#include "TestSensorsActivity.h"
#include "TestMotorsActivity.h"
#include "Program1Activity.h"
#include "Program2Activity.h"
#ifndef DISABLE_CATABRIGA
	#include "Catabriga.h"
#endif

#ifndef DISABLE_ZYGOTE
	MainActivity zygote = MainActivity();
#endif

Button v = Button();
Button back = Button();
SeekBar pb, pbup;

char c;
void serial(){

	if(PC.available() > 0){
		c = PC.read();

		if(!c)
		return;

        // Serial.print("$ thread: got: ");
        // Serial.println(c);
        Activity* act = ActivityManager::getCurrentActivity();
        if(c == 'p'){
            // Serial.print("$ Thread: pausing Activity: ");
            // Serial.println(act->ActivityID);
            act->pause();
            }else if(c == 'r'){
            // Serial.print("$ Thread: resuming Activity: ");
            // Serial.println(act->ActivityID);
            act->resume();
            }else if(c == 's'){
            // Serial.print("$ Thread: resuming Activity: ");
            // Serial.println(act->ActivityID);
            act->stop();
            }else if(c == 'k'){
            // Serial.print("$ Thread: resuming Activity: ");
            // Serial.println(act->ActivityID);
            act->kill();
            }else if(c == 'g'){
            	PC.print("$ Thread: Current Activity: ");
            	PC.println(act->ActivityID);
            // act->kill();
        }
    }
}

void setup(){  
	initRobot();

	Timer.getAvailable().attachInterrupt(serial).start(50);

	#ifndef DISABLE_ZYGOTE
		
		#ifndef DISABLE_PROGRAM1
			Program1Activity *program1 = new Program1Activity();
			zygote.activities->add(program1);
		#endif

		#ifndef DISABLE_CATABRIGA
			CatabrigaActivity *catabriga = new CatabrigaActivity();
			zygote.activities->add(catabriga);
		#endif

		Program2Activity *program2 = new Program2Activity();
		zygote.activities->add(program2);

		#ifndef DISABLE_IMU
			zygote.activities->add(new TestIMUActivity());
		#endif
		
		TestVictimActivity *testVictim = new TestVictimActivity();
		zygote.activities->add(testVictim);

		#ifndef DISABLE_SENSORS
			TestSensorsActivity *testSensors = new TestSensorsActivity();
			zygote.activities->add(testSensors);
		#endif

		#ifndef DISABLE_MOTION
			TestMotorsActivity *testMotors = new TestMotorsActivity();
			zygote.activities->add(testMotors);
		#endif


		zygote.o.x = 5;
		zygote.o.y = 5;
		zygote.initialize();
	#endif

	/*back.setArea(600,350,200,80);
	back.name = String("Return");
	back.onClick(goBack);
	act1.addView(&back);
	act2.addView(&back);
	act3.addView(&back);

	CheckBox *check = new CheckBox("Enable?");
	check->onChange(checkbox_changed);
	check->o = Point(30,10);
	act3.addView(check);

	CheckBox *check2 = new CheckBox("");
	check2->onChange(checkbox_changed);
	check2->o = Point(30,100);
	check2->w = 100;
	check2->h = 100;
	act3.addView(check2);

	// Progress bar testing
	Thread* updatPbBar = new Thread();
	updatPbBar->onRun(onUpdateProgress);
	updatPbBar->setInterval(0);
	act3.Threads.add(updatPbBar);

	pb = SeekBar();
	pb.o.x = 200;
	pb.o.y = 10;
	pb.w = 500;
	pb.h = 30;
	pb.setMax(100);
	act3.addView(&pb);

	pbup = SeekBar();
	pbup.o.x = 200;
	pbup.o.y = 250;
	pbup.w = 30;
	pbup.h = 200;
	pbup.type = ProgressBar::LINEAR_UP;
	// pbup.setMax(1.0);
	act3.addView(&pbup);*/



}

void loop(){
	PC.println("====== START OF PROGRAM ======");
    // Start Activity
    #ifndef DISABLE_ZYGOTE
    	zygote.start();
    #else
    	// Enter code here to run "custom" zygote
	#endif
    // End of Program
    PC.println("====== END OF PROGRAM ======");
}

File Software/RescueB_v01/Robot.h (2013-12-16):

#include <Arduino.h>

// Motors incluedes
// #include "MoveController.h"
// #include "mbed_driver.h"

// General peripheral includes
// #include <DueTimer.h>
// #include <UTouch.h>
// #include <UTFT.h>

// Operational System
// #include <ArduinOS.h>

// Include Icons and fonts
// #include <fGUI.c>

/*
	GLOBAL Sensors objects
*/
// IMU setup
#ifndef DISABLE_IMU
	IMUSensor *IMU;
#endif

// SENSORS setup
#ifndef DISABLE_SENSORS
	AnalogIn 	Light1 = AnalogIn(pLIGHT_IN1),
				Light2 = AnalogIn(pLIGHT_IN2),
				*Light[2];

	DigitalOut	LightLed = DigitalOut(pLIGHT_LED),
				VictimLed = DigitalOut(pLED_VICTIM);

	DistanceInterface 	*Dist[8];

	CompoundDistanceSensor 	*DistFront,
							*DistBack;

	DistanceInterface 	*DistLeftFront,
						*DistLeftBack,
						*DistRightFront,
						*DistRightBack;

	AngleEstimator 		*angleLeftEstimator,
						*angleRightEstimator;

	PoseEstimator 		*poseEstimator;

	DistanceEstimator 	*frontEstimator,
						*backEstimator;
#endif

/*
    MoveController definitions
*/
#ifndef DISABLE_MOTION
	MoveDriver *MD;
	MoveController *MC;
#endif

/*
    MoveController definitions
*/
#ifndef DISABLE_VICTIM
	VictimChecker *VICTIM;
#endif

/*
	LED Status timer interrupt
*/
/*void irqLedStatus(){
	static bool active = false;

	 PIO_SetOutput( g_APinDescription[pLED_STATUS].pPort, g_APinDescription[pLED_STATUS].ulPin, active, 0, PIO_PULLUP ) ;
}*/

/*
	RETURN Button implementation
*/
void irqReturnBtn(){
	Serial.println("$Return: callback requested");
	static long lastCall = 0;
	// Check if there was a minimum time between clicks (debounce)
	if(millis()- lastCall < osRETURN_MIN_TIME)
		return;

	lastCall = millis();
	ArduinOS::actionHandler(ACTION_RETURN);
}

/*
	Beep function and Thread
*/
// Used to warn battery
Thread thrBeeper;
void onBeeper(){
	static bool beeping = false;
	beeping = !beeping;
	digitalWrite(pBUZER, beeping);
	if(beeping)
		thrBeeper.setInterval(TIME_BEEP_H);
	else
		thrBeeper.setInterval(TIME_BEEP_L);
}

// Notify touchs
void beep(){
	digitalWrite(pBUZER, HIGH);
	delayMicroseconds(10000);
	digitalWrite(pBUZER, LOW);
}

/*
	Function reponsable for merging both LONG and SHORT
	distance sensors.
*/
long onCalculateDistance(long dist1, long dist2){
	if(dist1 >= 30)
		return dist2 + 7;
	return dist1 + 7;
}


#ifndef DISABLE_LCD
	/*
		LCD and Touch definitions
	*/
	UTFT LCD(ITDB50,pLCD_RS,pLCD_WR,pLCD_CS,pLCD_RESET);
	UTouch TCH = UTouch(pTCH_CLK,pTCH_CS,pTCH_DIN,pTCH_OUT,pTCH_IRQ);

	// extern uint8_t SmallFont[];			// Font
	// extern uint8_t BigFont[];		// Font
	extern uint8_t OCR_A_Extended_M[];	// Font
	// extern uint8_t SevenSegNumFont[];	// Font
	extern uint8_t fGUI[];				// Font


	/*
		System GUI (General User Interface)
	*/
	Thread thrUpdateGUI;
	View GUI = View();
	void onGUIupdate(){
		static float voltage, analog;
		static int batteryStatus, failsCount = 0;
		LCD.setBackColor(cGUITopBarFill);
		
		// Print BT status
		LCD.setFont(fGUI);
		LCD.setColor(180,180,180);
		LCD.printNumI(6, 1,1);
		

		// Calculates battery voltage and current status
		analog = analogRead(pVIN);
		voltage = max((analog-175)/86.25 + 6, 0);

		if(analog <= VOLTAGE_USB){
			batteryStatus = fGUI_USB;	// On USB
		}else{
			batteryStatus = 
				max(0,min(5,map(voltage*100, VOLTAGE_LOW*100, VOLTAGE_HIGH*100,
					0,5)));
		}

		if(batteryStatus == 0){
			if(++failsCount >= 3)
				thrBeeper.enabled = true;	// Enable Beeper thread
			LCD.setColor(240,20,30);	// Very low
		}else if(batteryStatus == fGUI_USB){
			LCD.setColor(70,70,70);		// USB Plugged
		}else if(batteryStatus >=  4){
			LCD.setColor(20,200,20);	// Full charge
		}else{
			LCD.setColor(245,210,95);	// Normal
		}

		if(batteryStatus != 0){
			thrBeeper.enabled = false;	// Disable Beeper thread
			digitalWrite(pBUZER, LOW); 	// Stop beeping
			failsCount = 0;
		}

		// Render Battery status
		LCD.printNumI(batteryStatus, 731,1);
		LCD.setFont(fTextBig);
		LCD.setColor(150,150,150);
		if(batteryStatus != fGUI_USB)
			LCD.printNumF(voltage,1, 665,4,'.',4);
		else
			LCD.print("USB",680,4);

		LCD.print(String(ArduinOS::cpuThreadUsage) + "%  ", 78,4);
	}
	
	void onGUIrender(){
		static Activity* act;
		act = ActivityManager::getCurrentActivity();

		LCD.setColor(cGUITopBarFill);
		LCD.fillRect(0,0,LCDWidth, 31);
		LCD.setBackColor(cGUITopBarFill);

		// Render Activity Name
		if(act){
			LCD.setColor(VGA_BLACK);
			LCD.setFont(fTextBig);
			LCD.print(act->ActivityName, CENTER, 4);
		}

		onGUIupdate();
		// PC.println("$: GUI: Rendered.");
	}

	View STAGE = View();
	void onSTAGErender(){
		LCD.setColor(VGA_BLACK);
		LCD.fillRect(ArduinOS::_rel.x,ArduinOS::_rel.y,LCDWidth, LCDHeight);
	}

	void onInvalidateView(){
		ArduinOS::requestRender = true;
	}

#endif	// DISABLE_LCD

ProgressBar preLoader = ProgressBar();
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

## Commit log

2013-12-16 General files upload
    [BOM-Template.xlsx, Custos-Geral.xlsx, Planilha de custos-RescueB.xlsx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]
2013-12-16 Electronics upload
    [Arduino DUE.PcbDoc, Arduino DUE.SchDoc, Bluetooth.SchDoc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]
2013-12-16 Export folder upload
    Exported files to laser cut, 3D print, interface with altium…
    [Board Outline.DWG, Board Outline.DXF, Chassi.STL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]
2013-12-16 Mechanics upload
    [Bateria-Lipo1.SLDPRT, Botão.SLDPRT, Cable_3-Robô_02.sldasm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]
2013-12-16 Midia files upload
    Banners, renders, infographics, t-shirts…
